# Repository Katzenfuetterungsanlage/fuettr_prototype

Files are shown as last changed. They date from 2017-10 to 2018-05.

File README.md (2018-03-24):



# Katzenfütterungsanlage

## fuettr_prototype

### Diplomarbeit

*Alle Rechte liegen bei den Schülern die sich mit dieser Arbeit auseinandersetzen!*

## Installation

<!-- ```bash
curl -sL https://deb.nodesource.com/setup_8.x | sudo -E bash -
```
```bash
sudo apt install -y git
``` -->

```bash
curl -L https://goo.gl/8vdw15 | bash
```

## Übertragungsprotokoll

[*klick*](https://github.com/Katzenfuetterungsanlage/fuettr_prototype/tree/master/Uebertragungsprotokoll#Übertragungsprotokoll)

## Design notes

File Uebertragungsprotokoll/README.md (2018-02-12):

# Übertragungsprotokoll

## Inhaltsverzeichnis

* [Server zu Client Kommunikation](#server-zu-client-kommunikation)
  * [1.1 Maschinenstatus](#11-maschinenstatus)
    * [Möglichkeitenbaum](#möglichkeitenbaum)
    * [Beispiel](#beispiel)
  * [1.2 Fütterungszeiten](#12-fütterungszeiten)
    * [Möglichkeitenbaum](#möglichkeitenbaum-1)
    * [Beispiel](#beispiel-1)
  * [1.3 Geräteinformationen](#13-geräteinformationen)
    * [Möglichkeitenbaum](#möglichkeitenbaum-2)
    * [Beispiel](#beispiel-2)
  * [1.4 Positions-info](#14-positions-info)
    * [Möglichkeitenbaum](#möglichkeitenbaum-3)
    * [Beispiel](#beispiel-3)
  * [1.5 Warnungen](#15-warnungen)
    * [Möglichkeitenbaum](#möglichkeitenbaum-4)
    * [Beispiel](#beispiel-4)
  * [1.6 Errors](#16-errors)
    * [Möglichkeitenbaum](#möglichkeitenbaum-5)
    * [Beispiel](#beispiel-5)
* [Client zu Server Kommunikation](#client-zu-server-kommunikation)
  * [2.1 Fütterungszeiten](#21-fütterungszeiten)
    * [Möglichkeitenbaum](#möglichkeitenbaum-6)
    * [Beispiel](#beispiel-6)
  * [2.2 Warnungen löschen](#22-warnungen-löschen)
    * [Möglichkeitenbaum](#möglichkeitenbaum-7)
    * [Beispiel](#beispiel-7)
  * [2.3 Errors löschen](#23-errors-löschen)
    * [Möglichkeitenbaum](#möglichkeitenbaum-8)
    * [Beispiel](#beispiel-8)

## Server zu Client Kommunikation

### 1.1 Maschinenstatus

| last_time | next_time | next_time_in | machine_state |
| --- | --- | --- | --- |
| string | string | string | string |

#### Möglichkeitenbaum

* last_time
  * 00:00 - 23:59
  * --:--
* next_time
  * 00:00 - 23:59
  * --:--
* next_time_in
  * 00:00 -23:59
  * --:--
* machine_state
  * An
  * Aus

#### Beispiel:

```JSON
{  
    "last_time" : "10:10",  
    "next_time" : "11:11",
    "next_time_in" : "00:10",
    "machine_state" : "Aus"
}
```

### 1.2 Fütterungszeiten

| time1  | time2  | time3  | time4  | time1_active | time2_active | time3_active | time4_active |
| --- | --- | --- | --- | --- | --- | --- | --- |
| string | string | string | string | boolean | boolean | boolean | boolean |

#### Möglichkeitenbaum

* time1
  * 00:00 - 23:59
* time2
  * 00:00 - 23:59
* time3
  * 00:00 - 23:59
* time4
  * 00:00 - 23:59
* time1_active
  * true/false
* time2_active
  * true/false
* time3_active
  * true/false
* time4_active
  * true/false

#### Beispiel:

```JSON
{  
    "time1":"11:11",
    "time2":"12:12",
    "time3":"13:13",
    "time4":"",
    "time1_active":true,
    "time2_active":false,
    "time3_active":true,
    "time4_active":false
}
```

### 1.3 Geräteinformationen

| serialnumber | internal | wlanState |
| --- | --- | --- |
| string | string | string |

#### Möglichkeitenbaum

* serialnumber
  * #000000 - #FFFFFF
* internal
  * Raspberry Pi 3 Model B
  * Raspberry Pi 2 Model B
  * ...
* wlanState
  * nicht verbunden
  * verbunden
  * ausgeschalten

#### Beispiel:

```JSON
{  
    "serialnumber" : "#000001",
    "internal" : "Raspberry Pi 3 Model B",
    "wlanState" : "disconnected"
}
```

### 1.4 Positions-info

| motor1 | motor2 | sensor1 | sensor2 |
| --- | --- | --- | --- |
| string | string | string  | string  |

#### Möglichkeitenbaum

* motor1 -
* motor2 -
* sensor1 -
* sensor2 -

#### Beispiel:

```JSON
{
    "motor1": "",
    "motor2": "",
    "sensor1": "",
    "sensor2": ""
}
```

### 1.5 Warnungen

| warnings   |
| ---------- |
| warning[ ] |

| warning | id |
| --- | --- |
| string  | number |

#### Möglichkeitenbaum

* warnings
  * warning
    * string
    * 1 - 65535

#### Beispiel

```JSON
{
    "warnings": [{
        "warning" : "Füllstand niedrig",
        "id": 65535
    },{
        "warning" : "Füllstand leer",
        "id": 5168
    }]
}
```

### 1.6 Errors

| errors   |
| -------- |
| error[ ] |

| error  | id |
| --- | --- |
| string | number |

#### Möglichkeitenbaum

* errors
  * error
    * string
    * 1 - 65535

#### Beispiel

```JSON
{
    "errors": [{
        "error": "Motor 2 blockiert",
        "id": 51644
    }]
}
```

## Client zu Server Kommunikation

### 2.1 Fütterungszeiten

| time1  | time2  | time3  | time4  | time1_active | time2_active | time3_active | time4_active |
| --- | --- | --- | --- | --- | --- | --- | --- |
| string | string | string | string | boolean | boolean | boolean | boolean |

#### Möglichkeitenbaum

* time1
  * 00:00 - 23:59
* time2
  * 00:00 - 23:59
* time3
  * 00:00 - 23:59
* time4
  * 00:00 - 23:59
* time1_active
  * true/false
* time2_active
  * true/false
* time3_active
  * true/false
* time4_active
  * true/false

#### Beispiel:

```JSON
{  
    "time1":"06:46",
    "time2":"12:55",
    "time3":"17:58",
    "time4":"23:01",
    "time1_active":false,
    "time2_active":true,
    "time3_active":true,
    "time4_active":true
}
```

### 2.2 Warnungen löschen

| id     |
| ------ |
| number |

#### Möglichkeitenbaum

* id
  * 1 - 65535

#### Beispiel

```JSON
{
    "id": 5618
}
```

### 2.3 Errors löschen

| id     |
| ------ |
| number |

#### Möglichkeitenbaum

* id
  * 1 - 65535

#### Beispiel

```JSON
{
    "id": 51644
}
```

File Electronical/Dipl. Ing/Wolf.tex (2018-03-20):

\lohead{Julian Wolf}
\chapter{Elektronik und Mechanik}
\label{sec:elektronik-und-mechanik}

\section{Anforderung Elektronik Variante 1}
\subsection{Aktoren}
Die Anforderungen der Aktoren im Elektrischen Teil, bestehen darin ein Förderband und eine Drehplatte zu drehen. Für beide Anwendungen werden Motoren mit einem hohen Drehmoment und einer niedrigen Drehzahl benötigt. Weiters dürfen sich die Motoren nicht drehen, wenn sie nicht angesteuert werden.
Zur Positionierung, Befestigung und durchführung anderer linearer Bewegungen werden weiteres Hubmagnete inf Form von Zylindermagneten benötigt. Diese Hubmagnete haben die Aufgabe Futterbeutel zu verschieben, zu positionieren, festzuhalten und einen Scherenhebel zum öffnen der Futterbeutel zu betätigen.  
\subsection{Sensoren}
Die Anforderung der Sensoren im Elektrischen Teil, bestehen darin erkennen zu können, ob ein Objekt vor ihnen steht. Dadurch kann überprüft werden, ob Futterschüsseln und Futterbeutel and der richtigen Stelle stehen, mögliche Fehler erkannt werdn und Zählungen der Futterschüsseln durchgeführt werden, damit erfasst werden kann, welche der fünf Futterschüsseln an welcher Position steht.
\subsection{Ansteuerungen}
Die Aufgabe der Ansteuerung ist es, möglichst einfach, günstig und sicher die Aktoren und Sensoren ansteuern zu können.

\section{Anforderung Elektronik Variante 2}
\subsection{Aktoren}
Die Anforderungen der Aktoren im Elektrischen Teil, bestehen darin ein Förderband und eine Drehplatte zu drehen. Für beide Anwendungen werden Motoren mit einem hohen Drehmoment und einer niedrigen Drehzahl benötigt. Weiters dürfen sich die Motoren nicht drehen, wenn sie nicht angesteuert werden.
\subsection{Sensoren}
Die Anforderung der Sensoren im Elektrischen Teil, bestehen darin erkennen zu können, ob ein Objekt vor ihnen steht. Dadurch kann überprüft werden, ob Futterschüsseln und Futterbeutel and der richtigen Stelle stehen, mögliche Fehler erkannt werdn und Zählungen der Futterschüsseln durchgeführt werden, damit erfasst werden kann, welche der fünf Futterschüsseln an welcher Position steht.
\subsection{Ansteuerungen}
Die Aufgabe der Ansteuerung ist es, möglichst einfach, günstig und sicher die Aktoren und Sensoren ansteuern zu können.

\section{Variante 1}
\subsection{Aktoren}
\subsubsection{Hubmagnete}
\begin{figure}[H] 
\begin{center}


\caption{Hubmagnet}
\label{Hubmagnet}

\end{center}
\end{figure}
Zylinderhubmagnete bestehen aus einem zylindrischen Dauermagnetkerns. Umgeben ist dieser Magnetkern von einer Spule und einem Gehäuse, welches das ganze Konstrukt vor Festkörpern schützt. Wird an die Spule eine Spannung angelegt, fließt ein Strom durch die Spule. Dieser Strom erzeugt ein Magnetfeld was den Magnetkern anzieht oder abstößt. Durch eine gezielte übersteuerung des Magnetzylinders, kann die Kraft des Magnetfeldes kurzzeitig verstärkt werden, jedoch verhindert die erhöhte Hitzeentwicklung einen dauerhaften Betrieb im übersteuerten Zustand. Der übersteuerte Zustand wird mit einer gerngeren relativen Einschaltdauer gegenüber der Zykluszeit bewirkt. Der Strom der durch die Spule fließt kann sich durch die kurze Einschaltdauer nicht einpendeln, was der Spule erlaubt mit einem durchschnittlich höheren Strom betrieben zu werden, was zu einem stärkeren Magnetfeld und somit zu einer stärkeren Kraft führt. Die genauen Werte der Kraft zur relativen Einschaltdauer lassen sich dem Datenblatt jedes einzelnen Hubmagnetens entnehmen. Ein Vorteil von Hubmagneten ist es, dass sie in allen möglichen Formen, Hublängen, Hubkräften und Wechsel- oder Gleichspannungsbereichen verfügbar sind. Hubmagnete können auch mit 3 verschiedenen Hubzuständen erworben werden. Monostabile Hubmagnete halten sich, mithilfe einer Feder, bei stromlosen Zustand immer an der Anfangs oder Endposition. Bistabile Hubmagnete verweilen im stromlosen Zustand an ihrer aktuellen Position, also entweder im eingefahrenen oder ausgefahrenen Zustand. Tristabile Hubmagnete bleiben, wie bistabile Hubmagnete, stromlos an ihrer aktuellen Postition. Jedoch kann diese Hubmagnetart auch an einer vorgegebenen Mittelposition verweilen.

\subsubsection{Motoren}
Nach einigen Problemen und Variantenänderungen in der Mechanik, wurde die Motorenauswahl erst in Variante 2 vorgenommen, da die Auswahl für Variante 1 sinnfrei wäre.

\subsection{Sensoren}
\begin{figure}[H] 
\begin{center}

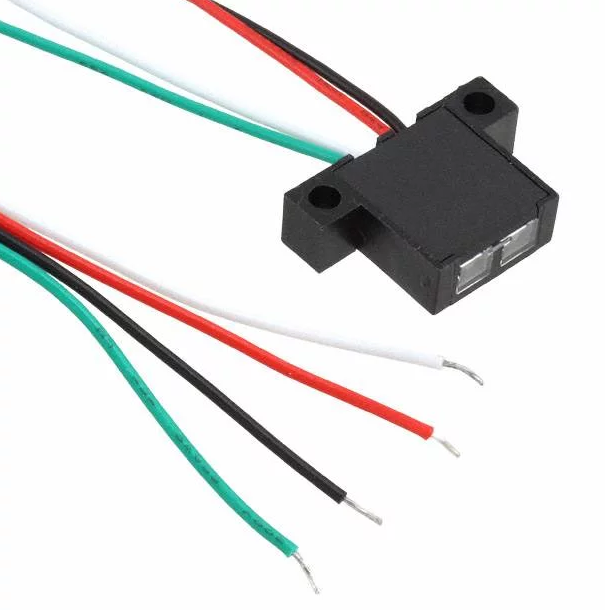
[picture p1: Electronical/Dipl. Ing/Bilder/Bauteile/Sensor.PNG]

\caption{Sensor}
\label{Sensor}

\end{center}
\end{figure}
Die Auswahl des Sensor für unsere Anwendung wurden von folgenden Kriterian beeinflusst: Befestingungsmöglichkeiten, Preis und zusätzlich benötigte Ansteuerungen.
Kapazitive und Induktive Näherungsschalter lassen sich einfach befestigen, sind jedoch nicht sehr günstig. Auch ist die Reichweite der Sensoren nicht sehr groß, was aber in unserer Anwendung unwichtig ist. Für diese Arten von Sensoren werden zusätzliche Ansteuerungen benötigt. Diese Ansteuerungen sind meistens teuer und benötigen zur Kommunikation mit einem Raspberry eine Schnittstelle.
Wir haben uns in diesem Anwendungsbereich für einen Optischen Näherungsschalter entschieden. Dieser beinhaltet ein fertiges Modul bestehend aus einer Infrarot LED und einem Infrarot Fototransistor. Diese Modul ist günstig und auch leicht zu befestigen. Dadurch, dass unsere Anwendung keine genaue Abstandsmessung benötigt, wird keine zusätzliche Ansteuerung benötigt. Zur Stromversorgung reichen 5V Gleichspannung mit einem laut Datenblatt berechneten Vorwiderstand. Die Auswertung erfolgt durch einen digitalen Input-Pins des Raspberrys. Sobald sich eine Reflektorfläche vor den Sensor bewegt, wird der Fototransistor niederohmig und ermöglicht somit einen Stromfluss. Dadurch liegt eine Spannung von 3,3V am Input-Pin an und wird vom Raspberry als High-Zustand angesehen. Wenn die Reflektorfläche vom Modul nicht mehr erfasst wird, sperrt der Fototransistor, der Stromfluss wird unterbunden und am Input-Pin liegen nurmehr 0V an, was als Low-Zustand angesehen wird.

\subsection{Ansteuerungen}
Da Variante 1 Nur kurze Zeit verfolgt wurde, wurden genaue Ansteuerungen für Motoren und Hubmagneten nicht herausgesucht. Der Sensor benötigt keine zusätzliche Ansteuerung

\section{Variante 2}
\subsection{Aktoren}
\subsubsection{Hubmagnete}
Für die zweite Variante werden keine Hubmagnete benötigt, da alle Befestigungen rein mechanisch erfolgen.

\subsubsection{Motoren}
\begin{figure}[H] 
\begin{center}

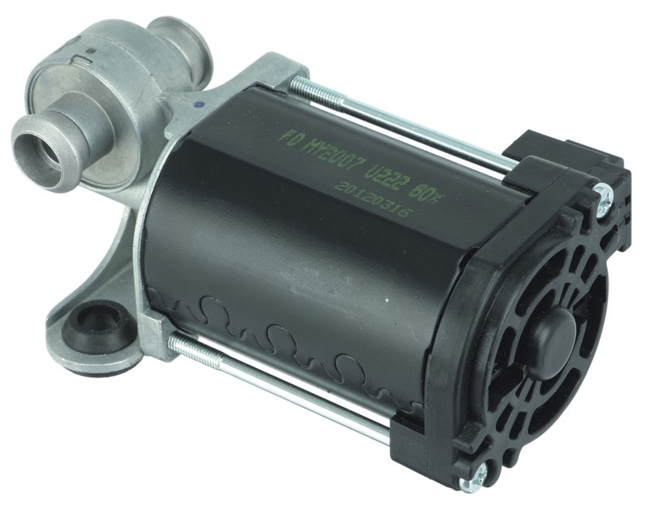
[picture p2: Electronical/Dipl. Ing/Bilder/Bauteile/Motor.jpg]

\caption{Motor}
\label{Motor}

\end{center}
\end{figure}
Die Motoren wurden mithilfe folgender Kriterien ausgesucht: Preis, Drehzahl, Kraft, stromloses Verhalten, Spannung.
In unserer Elektronik soll nur mit sicherer niedrieger Gleichspannung gearbeitet werden. Daher kommen nur Motoren mit einem Spannungsbereich von 0-24V in frage. Aus diesem Grund wird die Auswahl eines Asynchronmotors ausgeschlossen. Die Anwendung fordert, dass sich die Motoren im Stromlosen zustand nicht bewegen lassen. Dadurch können folgende Motorarten ausgeschlossen werden: Synchronmotoren, reine Gleichstrommotren, Schrittmotoren und Servomotoren, falls diese Motoren nicht über eine aktive Bremse verfügen. Ideal für unsere Anwendungen sind Gleichstrom-Schneckengetriebe-Motoren. Diese Motoren lassen sich aufgrund des mechanischen Auifbaus im stromlosen Zustand nicht drehen. Diese Motoren verfügen meistens auch über eine Getriebe was eine Übersetzung in eine niedrigere Drehzahl zur folge hat. Gleichzeitg wird mit diesem Getriebe auch das Drehmoment erhöht, weshalb der Motor eine höhere Kraft aufbringen kann. Zusätzlich werden Schneckengetriebemotoren in der Automobil Industrie als Scheibenwischermotoren verwendet. Daher sind diese Motoren sehr Preisgünstig zu erwerben.

\subsubsection{Lüfter}
\begin{figure}[H] 
\begin{center}

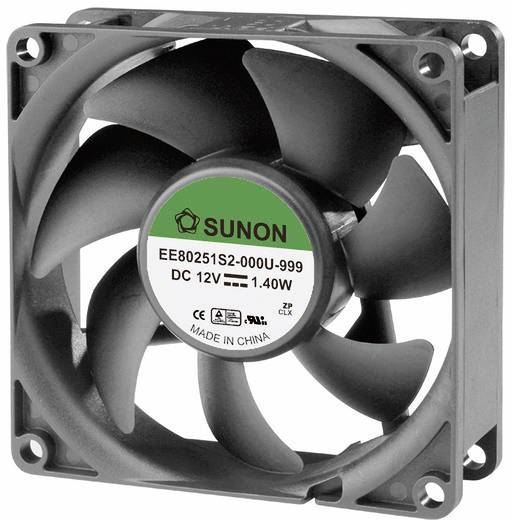
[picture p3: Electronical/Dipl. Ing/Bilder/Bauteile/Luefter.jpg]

\caption{Luefter}
\label{Luefter}

\end{center}
\end{figure}
Zur Kühlung des Raspberrys, wird ein externen 12V-Lüfter hergenommen, welcher einen Luftstrom um den Raspberry und den $\mu$Controller erzeugt.
\subsection{Sensoren}
Der ausgewählte Optische Sensor wurde in Variante 1 bereits beschrieben. Für genauere Informationen lesen Sie bitte in Punkt 1.3.2 nach.
Es werden zwei dieser Sensoren zur Positionierung verwendet. Der Sensor muss nur erkennen ob sich eine Reflektorfläche vor ihm befindet. Bei der Futterschüsseldrehplatte wird am Rand der Scheibe an der position jeder Futterschüssel ein Reflektorstreifen verwendet. Dadurch kann mit der Software gezählt und erkannt werden, welche Futterschüssel sich aktuell vor dem Sensor befindet. Im Futterbeutelmagazin wird der Sensor dazu verwendet um erkennen zu können ob ein Futterbeutel zum Füttern verfügbar ist. Wird vom Sensor, nach drehen des Motors, kein weiterer Futterbeutel erkannt, wird von der Software, falls nötig, ein Fehler ausgegeben und der Benutzer wird informiert. Der Reflektorstreifen wird auf der Verschlussklemme jedes Futterbeutels befestigt.
\subsection{Ansteuerung}
Der Gesamtschaltplan wurde in ProfiCad realisiert. Der Schaltplan beinhaltet die Ansteuerung der Motoren und Sensoren, sowie die Visualisierung der Verkabelung der einzelnen Elemente.
Für ein einfacheres Verständnis wird der Gesamtschaltplan in kleinere Elemente aufgeteilt und in Unterpunkten beschrieben
\subsubsection{Motoransteuerung Variante 1}
Gleichstrom Schneckengetriebemotoren haben die Fähigkeit sich in beide Richtungen zu drehen, je nach polarität der Anschlüsse. Um eine Softwaretechnische einfache Ansteuerung ermöglichen zu können, wird oft eine H-Brücke zur ansteuerung der Motoren verwendet. Diese H-Brücke besteht aus vier Transistoren. Für Motoren mit höheren Stromanforderungen werden MOSFET-Transistoren verwendet. Die Schaltung besteht aus zwei P-Kanal MOSFET T1, T2 beziehungsweise T5, T7 und aus zwei N-Kanal MOSFET T2, T4 beziehungsweise T6, T8. Die MOSFET und die Grundlegende Schaltung wurde von HIER ZITAT EINFÜGEN übernommen. Die P-Kanal 
\subsubsection{Motoransteuerung Variante 2}
\begin{figure}[H] 
\begin{center}

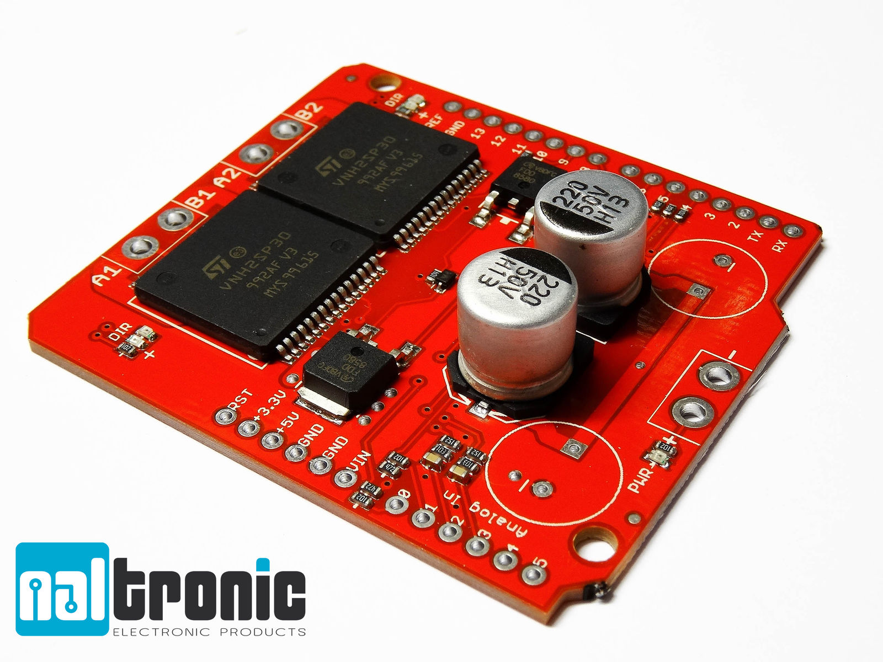
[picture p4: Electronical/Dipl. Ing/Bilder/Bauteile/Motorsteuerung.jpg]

\caption{Motorsteuerung}
\label{Motoransteuerung}

\end{center}
\end{figure}
Aus Sicherheits- und Kostentechnischen Gründen, wurde von einer manuell gesteuerten H-Brücke auf ein fertiges Motorsteuerungsmodul umgestiegen. Der Vorteil dieser Ansteuerung besteht darin, dass ein Kurzschluss der H-Brücke Hardwaretechnisch ausgeschlossen werden kann und damit nicht vond er Software abgesichert werden muss. Das Motormodul verfügt außerdem über eine Interne Strommessung für jeden der 2 unterstützten Motoren. Diese Messung kan bei bedarf abgefragt werden. Für unsere Anwendung ist dies jedoch nicht erforderlich. Der Mototreiber unterstützt 2 Motoren, welche mit bis zu 30 Ampere bei 16V betrieben werden können, bevor der IC überhitzt oder andere Bauteile zerstört werden. Die Ansteuerung jedes Motors erfolgt über ein Digitales Signal. Motor 1 kann über den Pin AI0 aktiviert(enabled) werden. Dies dient zur Sicherung das der Motor nicht ausversehen betätigt werden kann, solange der AI0 Pin nicht auf HIGH ist. Der enable Pin für Motor 2 ist AI1. Um Motor 1 in Uhrzeigersinn drehen zu lassen, muss der Pin D7 mit einem HIGH Signal und der Pin D8 mit einem LOW SIgnal angesteuert werden. Um Motor 2 gegen den Uhrzeigersinn drehen zu lassen, muss der Pin D8 mit einem HIGH Signal und der Pin D7 mit einem LOW Signal angesteuert werden. Um den Motor 1 bremsen zu können, muss Pin D8 und D7 mit entweder einem HIGH oder einem LOW Signal angesteuert werden. Für Motor 2 ist die Funktionsweise gleich jedoch muss der Pin D7 mit Pin D4 und Pin D8 mit Pin D9 ersetzt werden. Die externe Stromversorgung für den IC von 5V erfolgt über den VCC Pin. Die externe Stromversorgung für die Motoren erfolgt über den PWR Pin. Weiters muss der GND Pin noch mit einem der beiden Ground Anschlüsse der externen Stromversorgungen verbunden werden. Motor 1 wird über die Outputs A1 und B1 versorgt. Motor 2 wird über die Outputs A2 und B2 versorgt. Beim Anschluss der Motoren muss auf die Polung geachtet werdne und gegebenenfalls auch getestet werden, ob sich die Motoren auch wirklich beim Ansteuern der D7 oder D4 Pins in Uhrzeigersinn drehen und nicht gegen der Uhrzeigersinn. Falls beim Motor gekennzeichnet, sollte der Pluspol des Motors mit dem A1 beziehungsweise dem A2 Pin verbunden werden. Der Motortreiber verfügt auch über eine interne Drehzahlregelung, welche extra für beide Motoren über zwei PWM Input Pins gesteuert werden können. Die Drehzahl kann über den Duty Cycle des PWM Signals geregelt werden.
\subsubsection{PWM-Signal erzeugung für Motoransteuerung}
Ein PWM Signal ist ein periodisches Rechteck Signal. Eine Periode wird als Duty Cycle bezeichnet. Dieser Duty Cycle enthält eine Prozentangabe. Diese Prozentangabe sagt aus, wie viel Prozent des Duty Cycles HIGH und wie viel Prozent LOW sind. Ein Signal mit einem Duty Cycle von 100\% sagt aus, das eine Periodendauer zu 100\% aus einem HIGH Signal und zu 0\% aus einem LOW Signal besteht. Ein Duty Cycle von 25\% sagt aus, Das eine Periode zu 25\% aus einem HIGH Signal und zu 75\% aus einem LOW Signal besteht. Das PWM Signal kann von manchen ICs intern aufgenommen und der Duty Cycle ausgemessen werden. Dabei muss jedoch beachtet werden, dass die Frequenz des PWM Signals nicht die maximale Lesefrequenz des ICs übersteigt. Meistens wird diese Frequenz, wie bei unserem Motortreiber, im Datenblatt angegeben. Das PWM kann entweder über eigene ICs mit PWM Generatoren oder $\mu$Cs mit internen PWM Generatoren erzeugt werden. Das System muss nur über eine echtzeitfähigkeit besitzen, damit der Duty Cycle keine takte beim Zählen überspringen und damit nicht die frequenz fehlerhaft werden kann. 
Unser PWM Generator wurde mithilfe eines Arduino Nanos realisiert. Mithilfe des $\mu$C Atmega328P wird der Interne Zähler (Timer 2) dazu verwendet einen Output Pin in den richtigen Abständen zu toggeln (von HIGH auf LOW oder umgekehrt schalten) um ein PWM Signal zu erzeugen.

\begin{itemize}
\item verwendete Register:
\begin{itemize}
\item TCCR2A: Im TCCR2A Register wird festgelegt, in was für einem Modus der Timer laufen soll und was mit den Pins OC2A und OC2B passieren soll, wenn der der aktuelle Timer-Wert mit einem der beiden Output Compare Register übereinstimmt. Die Bits COM2A1 und COM2A0 setzen im Fast-PWM Modus fest, ob der OC2A Pin nicht beeinflusst wird und nicht verbunden ist, vom WGM22 Bit Abhängig ist, oder bei einem Compare Match, also wenn das Output Compare Register OCR2A mit dem Aktuellen Timer Wert übereinstimmt, der OC2A Pin gesetzt und beim reset des Timers resetet wird (non-inverting Mode), oder bei einem Compare Match der OC2A Pin resetet und beim reset des Timers gesetzt wird (inverting Mode). \\ Die selbe Funktion haben die Bits COM2B1 und COM2B0, nur dass der Pin OC2B verändert und mit dem Compare Registe OCR2B verglichen wird. \\
Die Bits WGM21 und WGM20 setzen den Modus des Signalgenerators die vom Timer unterstützt werden. Es gibt grundsätzlich 3 Modi in denen der Signalgenerator laufen kann: CTC, Fast PWM, PWM Phase Correct. \\
\begin{itemize}
\item Im CTC Modus kann der TOP Wert zu dem der Counter zählt, immer bei jedem vollständigen Zählvorgang geändert werden. Der Zähler zählt in Form eines Sägezahn Signals und toggled den Pin immer, wenn der Top Wert erreicht wird.\\
\item Im Fast PWM Modus zäjlt der Zähler in Form eines Sägezahnsignals und es wird bei jedem Zählschritt überprüft, ob der aktuelle Wert des Zählers mit dem Output Compare Register übereinstimmt. Was passiert, wenn die Werte übereinstimmen, wird in den COM2xx Bits festgelegt. Die Frequenz des Ausgangssignals am Pin kann nur über einen Prescaler verändert werden. Das bedeutet, dass die Frequenz nur 7 Frequenzen, mit dem internen Timer, annehmen kann. Das OCR2x Register kann während des betriebes geändert werden. Damit kann der Duty Cycle während des Betriebes geändert werden. \\
\item Der PWM Phase Correct Modus, lasst den Zähler von Bottom zu Top und wieder zu Bottom zählen. Das bewirkt, das er Zähler in Form eines Dreiecksignals zählt. Daher ist das Ausgangs PWM Signal immer symetrisch um den BOTTOM und TOP Wert des Zählers. Daher bleibt das Signal immer Phasenkorrekt. Der Nachteil dieses Modus ist, dass er nur die halbe Frequenz des Fast PWM Modus erreichen kann. Der PWM Phase Correct Modus, kann auch nur 7 Frequenzen annehmen.\\
\end{itemize} 
\item TCCR2B: Im TCCR2B Register wird für unsere Anwendung der Prescaler festgelegt um die frequenz des PWM-Signales einzustellen. Dazu werden die Bits 0 bis 2 verwendet. Das sind die Bits CS20, CS21 und CS22. Die Bits FOC2A, FOC2B und WGM22 werden in unserer Anwendung nicht benötigt und können ignoriert werden. \\
\item OCR2A: Das Register OCR2A ist das Output Compare Match Register für den OC2A Pin. Das Register kann einen Wert zwischen 0 und 255 haben wobei, im Fast PWM Modus, 0 einem Duty Cycle von 0\% und 255 einem Duty Cycle von 100\% entspricht.\\
\item OCR2B: Das Register OCR2B ist das Output Compare Match Register für den OC2B Pin. Das Register kann einen Wert zwischen 0 und 255 haben wobei, im Fast PWM Modus, 0 einem Duty Cycle von 0\% und 255 einem Duty Cycle von 100\% entspricht.\\
\item DDRD: Im Register DDRD können I/O Pins als Output Pins gesetzt werden. Es muss nur das Bit des entsprechenden Pins gesetzt werden.\\
\item DDRB: Im Register DDRB können I/O Pins als Output Pins gesetzt werden. Es muss nur das Bit des entsprechenden Pins gesetzt werden.\\
\end{itemize}
\item Frequenz berechnen:\\
Die maximal Frequenz des PWM-Signals für die Motoransteuerung beträgt 20kHz. Das bedeutet das man einen Frequenzwert so nahe wie mögliche, aber unter der Maximalen Frequenz wählen soll.\\
Berechnen lässt sich die Frequenz des PWM-Signals mit folgender Formel:
\begin{align*}
f_{OC2xPWM}=\frac{f_{clk\_I/O}}{N*256} \\
\end{align*} 
f$_{OC2xPWM}$ ist die Frequenz die das PWM-Signal haben wird.\\
f$_{clk_I/O}$ ist die Taktfrequenz des Atmega328P. Also 16MHz. \\
N ist der Wert des Prescalers, welcher im TCCR2B Register festgelegt wird. \\

\textbf{Frequenz berechnung:}\\
$f_{OC2xPWM}$=$\frac{f_{clk\_I/O}}{N*256}$ = $\frac{16000000}{8 \cdot 256}$ = $\underline{7812,5Hz}$
\item Programm für Atmega328P: \\
\begin{lstlisting}[caption=$\mu$C-Programm,language=c]
void app_main (void)
{
  DDRD = (1<<PD3);
  DDRB = (1<<PB3);
  TCCR2A = (1<<COM2A1) | (1<<COM2B1) | (1<<WGM21) | (1<<WGM20);
  TCCR2B = (1<<CS21);
  OCR2A = 0x5f;
  OCR2B = 0x5f;
  
}
\end{lstlisting}

\begin{itemize}
\item DDRD: Im DDRD Register wird der PD3 Pin auf Output geschaltet.\\
\item DDRB: Im DDRB Register wird der PB3 Pin auf Output geschaltet.\\
\item TCCR2A: Im TCCR2A Register wird der non-Inverting Fast-PWM Modus eingestellt für OC2A und OC2B. \\
\item TCCR2B: Im TCCR2B Register wird der Prescaler festgelegt. \\
\item OCR2A: Im OCR2A Register wird der Duty Cycle festgelegt. 0 entspricht 0\% und 255 entspricht 100\% \\
\item OCR2B: Im OCR2B Register wird der Duty Cycle festgelegt. 0 entspricht 0\% und 255 entspricht 100\% \\
\end{itemize}
\end{itemize}

\begin{figure}[H] 
\begin{center}

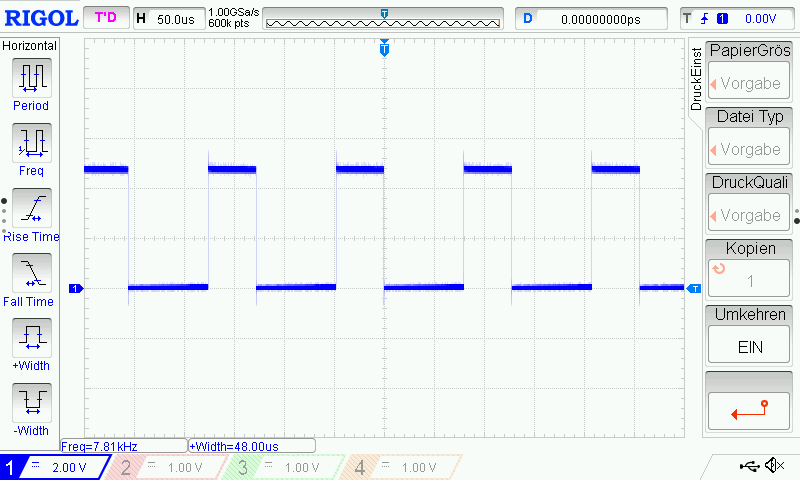
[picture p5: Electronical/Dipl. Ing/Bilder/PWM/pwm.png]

\caption{PWM}
\label{PWM}

\end{center}
\end{figure}
\newpage
\subsubsection{Gesamtschaltplan}
\begin{figure}[H] 
\begin{center}

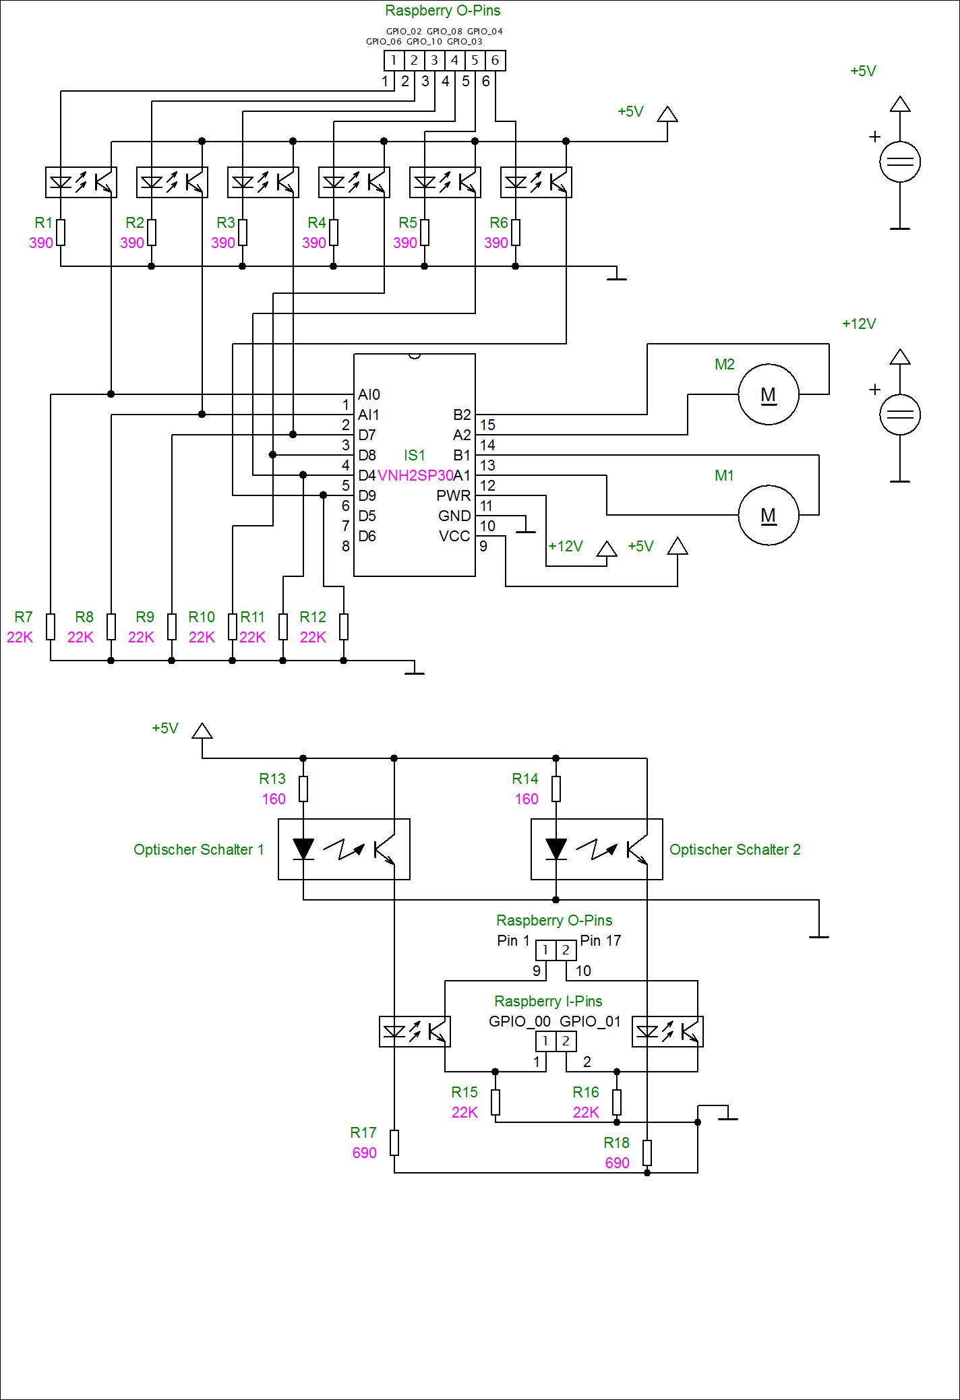
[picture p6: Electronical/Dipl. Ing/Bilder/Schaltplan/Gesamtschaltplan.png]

\caption{Gesamtschaltplan}
\label{Gesamtschaltplan}

\end{center}
\end{figure}
\subsubsection{Verkabelung der Motoransteuerung mit dazugehörigen Elementen}
\begin{figure}[H] 

\begin{center}

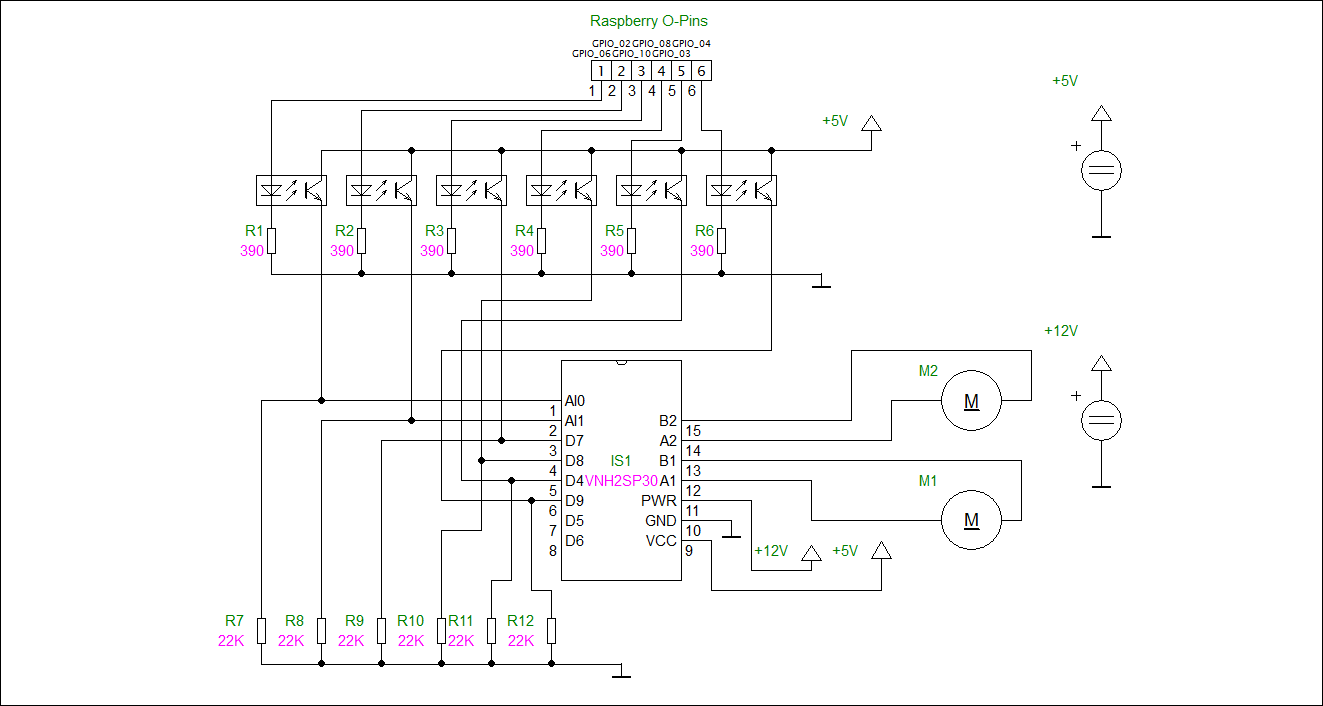
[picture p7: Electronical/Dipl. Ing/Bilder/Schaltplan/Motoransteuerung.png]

\caption{Motoransteuerung}
\label{Motoransteuerung}
\end{center}
\end{figure}
Die Motoransteuerung besteht aus folgenden Komponenten:\\
\begin{itemize}
\item Dem Motortreiber mit dem IC VNH2SP30.
\item Der Klemme Raspberry O-Pins, welche die GPIO-Pins des Raspberrys zur darstellung ersetzt.
\item Sechs Optokopplern, welche die Ausgangsspannung von den GPIO-Pins auf 5V bringt und die Raspberry-Pins vom restlichen Stromkreis galvanisch trennt.
\item Einem PWM-Generator in Form eines $\mu$Cs, welcher die Drehzahl der beiden Motoren steuert.
\item Den beiden Motoren M1 und M2.
\item Den Widerständen R1 bis R6, welche einen Spannungsabfall erzeugen, damit der Optokoppler nicht überlastet wird.
\item Den Pulldown-Widerständen R7 bis R12 welche ein floaten, also eine fehlerhafte Spannung an den Input-Pins der Motorsteuerung, verhindern sollen.
\item Den externen Spannungsversorgungen von 5V und 12V\\
\end{itemize}
\textbf{Genereller Ablauf:}
\begin{enumerate}
\item Der PWM Generator erzeugt ein Dauerhaftes PWM-Signal, welches an die PWM-Inputs D6 und D5 der Motoransteuerung gelegt wird.
\item Die GPIO-Pins geben ein High-Signal von 3,3V aus, welches die Optokoppler ansteuert. 
\item Der Optokoppler schaltet seinen internen Phototransistor durch und ermöglicht einen Stromfluss.
\item Dadurch, dass der Strom über die Optokoppler jetzt fließen kann, fließt ein Strom von der 5V Spannungsversorgung über den Optokpoppler in den Input-Pin der Motoransteuerung.
\item Je nach ansteuerung der Pins, dreht sich einer oder beide Motoren, in oder gegen den Uhrzeigersinn, oder werden gebremst. Dabei fließt ein Strom von der 12V Spannungsversorgung über die Motoransteuerung zu den Motoren.
\item Die Motoransteuerung regelt die Spannung an den Motoren mittels des PWM-Signals und regelt auch die Drehrichtung der Motoren je nach ansteuerung.
\end{enumerate}
\textbf{Berechnungen:}
\begin{itemize}
\item R1 bis R6: \\
Die Spannung die abfallen muss, und der Strom der fließt, kann aus dem Datenblatt des Optokopplers entnommen werden.\\
$U_{Optokoppler}=$1,15V \\
$U_{Optokoppler-max}=$1,4V \\
$I_{Optokoppler}$=5mA \\

\begin{center}
$R_{1,2,3,4,5,6}=\frac{U}{I}=\frac{U_{GPIO}-U_{Optokoppler}}{I_{Optokoppler}}=\frac{3,3V-1,15V}{0,005A}=430\Omega$
\end{center}
Da 430$\Omega$ kein E12-Wert ist, wird ein 390$\Omega$ Widerstand hergenommen.
Zur überprüfung, ob dieser Wert angenommen werden kann, muss die Spannung am Optokoppler neu gerechnet und überprüft werden, ob die Spannung zwischen der maximal zuläassige und der normalen Spannung ist.
\begin{center}
$U_{Optokoppler}=U_{GPIO}-(R_{1,2,3,4,5,6} \cdot I_{optokoppler})=3,3V-(390\Omega \cdot 0,005A) = 1,35V < U_{Optokoppler-max}$
\end{center}
Da die tatsächliche Spannung zwischen der maximalen und normalen Spannung des Optokopplers ist, ist dieser Widerstandswert zulässig.\\
\item R7 bis R12:\\
Diese Widerstandswerte werden mit 22k$\Omega$ angenommen.
\end{itemize}

\subsubsection{Verkabelung des Sensors mit dazugehörigen Elementen} 
\begin{figure}[H] 
\begin{center}

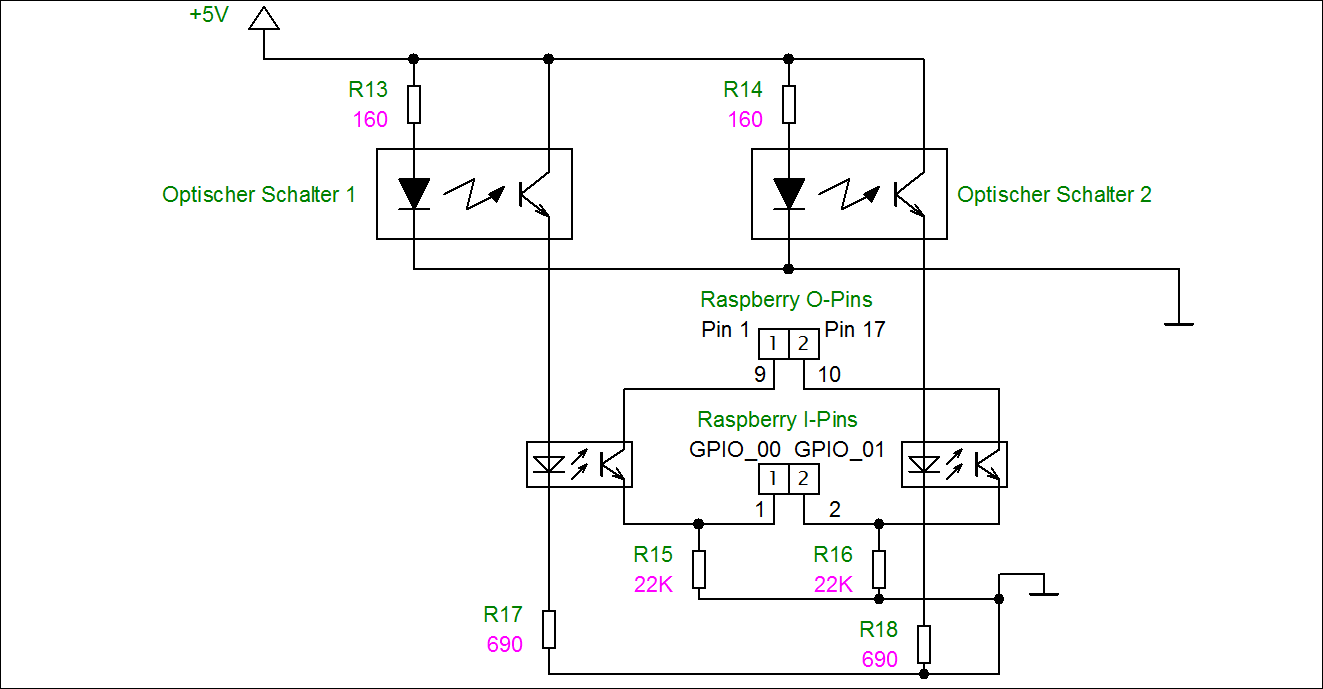
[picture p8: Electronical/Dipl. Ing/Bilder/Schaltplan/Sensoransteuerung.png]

\caption{Sensoransteuerung}
\label{Sensoransteuerung}

\end{center}
\end{figure}

Die Sensoransteuerung besteht aus folgenden Komponenten:
\begin{itemize}
\item Den optischen Sensoren OPB732WZ.
\item Der Klemme Raspberry O-Pins, welche die 3,3V-Pins des Raspberrys zur darstellung ersetzt.
\item Der Klemme Raspberry I-Pins, welche die GPIO-Pins des Raspberrys zur darstellung ersetzt.
\item Zwei Optokopplern, welche die Spannung der Sensoren von 5V auf ein 3,3V Potenzial bringen.
\item Den Widerständen R13 und R14, welche einen Spannungsabfall erzeugen, damit der Sensor nicht überlastet wird.
\item Den Widerständen R17 und R18, welche einen Spannungsabfall erzeugen, damit der Optokoppler nicht überlastet wird.
\item Den Pulldown-Widerständen R15 und R16 welche ein floaten, also eine fehlerhafte Spannung an den Input-Pins des Raspberrys, verhindern sollen.
\item Der externen Spannungsversorgunge von 5V\\
\end{itemize}
\textbf{Genereller Ablauf:}
\begin{enumerate}
\item Wenn der Sensor eine Reflektor-Fläche vor sich erkennt, schaltet der Phototransistor im Sensor durch.
\item Der durchgeschaltete Phototransistor, ermöglich einen Stromfluss von der Spannunsguelle in den Optokoppler.
\item Dadurch schaltet der interne Phototransistor des Optokopplers durch.
\item Der durchgeschaltete Phototransistor, ermöglich einen Stromfluss von einem der 3,3V-Pins in einen der GPIO-Pins des Raspberrys.
\item Somit kann erkannt werden, welcher der Sensoren eine Reflektor-Fläche erkennt und weitere Softwaretechnische Maßnahmen können erfolgen.
\end{enumerate}
\textbf{Berechnungen:}
\begin{itemize}
\item R17 und R18: \\
Die Spannung die abfallen muss, und der Strom der fließt, kann aus den Datenblättern des Sensors und des Optokopplers entnommen werden.\\
$U_{Optokoppler}=$1,15V \\
$U_{Optokoppler-max}=$1,4V \\
$U_{CE(SAT)}=$0,4V \\
$I_{Optokoppler}$=5mA \\

\begin{center}
$R_{13,14}=\frac{U}{I}=\frac{U_{5V}-U_{Optokoppler}-U_{CE(SAT)}}{I_{Optokoppler}}=\frac{5V-1,15V-0,4V}{0,005A}=690\Omega$
\end{center}
Da 690$\Omega$ kein E12-Wert ist, wird ein 680$\Omega$ Widerstand hergenommen.
Zur überprüfung, ob dieser Wert angenommen werden kann, muss die Spannung am Optokoppler neu gerechnet und überprüft werden, ob die Spannung  zwischen der maximal zuläassige und der normalen Spannung ist.
\begin{center}
$U_{Optokoppler}=U_{5V}-U_{CE(SAT)}-(R_{13,14} \cdot I_{optokoppler})=5V-0,4V-(680\Omega \cdot 0,005A) = 1,2V => U_{Optokoppler} < 1,2V < U_{Optokoppler-max}$
\end{center}
Da die tatsächliche Spannung zwischen der maximalen und normalen Spannung des Optokopplers ist, ist dieser Widerstandswert zulässig.\\
\item R13 und R14:\\
Die Spannung die abfallen muss, und der Strom der fließt, kann aus dem Datenblatt des Sensors entnommen werden.\\
$U_{F}=$1,8V \\
$I_{F}$=20mA \\

\begin{center}
$R_{13,14}=\frac{U}{I}=\frac{U_{5V}-U_{F}}{I_{F}}=\frac{5V-1,8V}{0,02A}=160\Omega$
\end{center}
Da 160$\Omega$ kein E12-Wert ist, wird ein 180$\Omega$ Widerstand hergenommen.
Zur überprüfung, ob dieser Wert angenommen werden kann, muss die Spannung am Optokoppler  neu gerechnet werden und überprüft werden, ob die Spannung geringer als die maximal zuläassige Spannung ist.
\begin{center}
$U_{F}=U_{5V}-(R_{13,14} \cdot I_{F})=5V-(180\Omega \cdot 0,02A) = 1,4V$
\end{center}
Da 1,4V die Spannung U$_{F}$ zu sehr unterschreiten würde, wird eine Seriellschaltung von einem 150$\Omega$ und einem 10$\Omega$ Widerstand benötigt.
\item R15 und R16:\\
Diese Widerstandswerte werden mit 22k$\Omega$ angenommen.
\end{itemize}

\section{Mechanische Konstruktion}
\subsection{Motorhalterung Futterschüsseldrehplatte}
\subsection{Motorhalterung Förderband}
\subsection{Sensorhalterung Futterschüsseldrehplatte}
\subsection{Sensorhalterung Förderband}
\subsection{Halterung Raspberry und $\mu$C}
\subsection{Lüfterhalterung für Raspberry}
\newpage
\section{Stückliste}
\begin{tiny}
\begin{center}
\begin{tabular}{|p{2cm}|c|c|p{3cm}|p{7cm}|} \hline
Name & ID & Stückzahl & Anmerkung & Link \\ \hline
Optek Optischer Näherungsschalter & OPB732WZ & 2 & - & \url{https://at.rs-online.com/web/p/products/9087113/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} \\ \hline 
Optokoppler & SFH6916 & 2 & 4 Optokoppler pro Bauteil & \url{https://www.neuhold-elektronik.at/catshop/product_info.php?products_id=4181} \\ \hline
Motorsteuerung & VNH2SP30 & 1 & Fertiges Modul aus 2 ICs und zusätzlicher Beschaltung & \url{https://www.ebay.at/itm/30A-VNH2SP30-Dual-Stepper-Motor-Driver-Monster-Moto-Shield-Module-Motortreiber/122543212784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} \\ \hline
Gleichstrom Motor & FD MY2007 U222 60x & 2 & Schneckengetriebe & \url{https://www.neuhold-elektronik.at/catshop/product_info.php?cPath=96_99&products_id=5522} \\ \hline
Schaltnetzteil 5V & ASTEC LPS42 & 1 & 11A & \url{https://www.neuhold-elektronik.at/catshop/product_info.php?cPath=114_118&products_id=6596} \\ \hline
Schaltnetzteil 12V & - & 1 & 30A & \url{https://www.optonicaled.at/netzeil-metal-360w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} \\ \hline
Lüfter 12V & EE80251S2-0000-999 & 1 & 80x80x25mm & \url{https://www.conrad.at/de/axialluefter-12-vdc-6286-mh-l-x-b-x-h-80-x-80-x-25-mm-sunon-ee80251s2-0000-999-323905.html} \\ \hline
Widerstand & - & 6 & Kohleschicht 390$\Omega$ & \url{https://www.conrad.at/de/kohleschicht-widerstand-390-axial-bedrahtet-0204-01-w-5-tru-components-1-st-1557169.html} \\ \hline
Widerstand & - & 2 & Kohleschicht 150$\Omega$ & \url{https://www.conrad.at/de/kohleschicht-widerstand-150-axial-bedrahtet-0204-01-w-5-1-st-400157.html} \\ \hline
Widerstand & - & 2 & Kohleschicht 10$\Omega$ & \url{https://www.conrad.at/de/kohleschicht-widerstand-10-axial-bedrahtet-0207-025-w-5-yageo-cfr-25jt-52-10r-1-st-1417641.html} \\ \hline
Widerstand & - & 2 & Kohleschicht 680$\Omega$ & \url{https://www.conrad.at/de/kohleschicht-widerstand-680-axial-bedrahtet-0207-025-w-5-yageo-cfr-25jt-52-680r-1-st-1417677.html} \\ \hline
Widerstand & - & 8 & Kohleschicht 22k$\Omega$ & \url{https://www.conrad.at/de/kohleschicht-widerstand-22-k-axial-bedrahtet-0207-025-w-5-yageo-cfr-25jt-52-22k-1-st-1417666.html} \\ \hline
Arduino Nano & - & 1 & Atmega328P zur PWM generierung & \url{https://www.amazon.de/AptoFun-Org-ATmega328P-FT232RL-Development-kompatibel/dp/B014TE52RS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} \\ \hline
\end{tabular}
\end{center}
\end{tiny}

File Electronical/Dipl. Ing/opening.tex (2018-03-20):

\frontmatter
\pagenumbering{Roman}
\addtocounter{page}{2}

\rehead{}
\ohead[\pagemark]{\pagemark}

\newcommand{\doublesignature}[1]{%
  \parbox{\textwidth}{
    \hfill
    \parbox{7cm}{
      \centering
      \rule{6cm}{1pt}\\
      Florian Greistorfer
    }
    \parbox{7cm}{
      \centering
      \rule{6cm}{1pt}\\
      Florian Harrer
    }
  }
}
\newcommand{\doublesign}[1]{%
\mbox{}\\
\mbox{}\\
\mbox{}\\
\mbox{}\\
  \parbox{\textwidth}{
    \hfill
    \parbox{7cm}{
      \centering
      \rule{6cm}{1pt}\\
      Dominik Pichler
    }
    \parbox{7cm}{
      \centering
      \rule{6cm}{1pt}\\
      Julian Wolf
    }
  }
}

\vspace*{20pt}

\section*{Eidestattliche Erklärung}
\label{sec:eidestattliche-erklaerung}
Ich erkläre an Eides statt, dass ich die vorliegende Arbeit selbstständig verfasst, andere als die angegebenen
Quellen/Hilfsmittel nicht benutzt und die den benutzten Quellen wörtlich und inhaltlich entnommenen
Stellen als solche kenntlich gemacht habe.\\
\\
Arnfels, am 5. April 2018\\

\vskip 1cm

\doublesignature{}
\doublesign{}

\vskip 5cm

\clearpage

\newpage
\thispagestyle{empty}
\mbox{}

\clearpage

\section*{Danksagung}
\label{sec:danksagung}
@TODO

\clearpage

\newpage
\thispagestyle{empty}
\mbox{}

\clearpage

\section*{Abstract}
\label{sec:abstract}
WULF!!!

\section*{Zusammenfassung}
WOLF!!!

\clearpage

\newpage
\thispagestyle{empty}
\mbox{}

\clearpage

\subsection*{Gender Erklärung}
\label{sec:gender-erklaerung}
Aus Gründen der besseren Lesbarkeit wird in dieser Arbeit die Sprachform des generischen Maskulinums angewendet. Es wird an dieser Stelle darauf hingewiesen, dass die ausschließliche Verwendung der männlichen Form geschlechtsunabhängig verstanden werden soll.

\subsection*{Über dieses Dokument}
\label{sec:ueber-dokument}
Diese Arbeit wurde in \LaTeX{} verfasst. Diese Art der Dokumentation bietet gegenüber den normalen Textverarbeitungen gewisse Vorteile hinsichtlich der Formatierung und des Einbindens von Grafiken. Auch Formeln können sehr einfach und effizient angegegeben werden. Die Rohfassung des Dokuments befindet sich auf Github.

\subsection*{Erklärung der Sprachen}
\label{sec:sprachen-erklaerung}
Da Teile dieser Arbeit über Programmieren sind und alle Dokumentationen und Fachbegriffe hauptsächlich auf Englisch zu finden sind, werden in diesen Teilen sehr viele Englischen Wörter verwendet.

\clearpage

\newpage
\thispagestyle{empty}
\mbox{}

\clearpage

\section*{Projektteam}
\label{sec:projektteam}

\subsection*{Florian Greistorfer}
\begin{wrapfigure}[12]{l}{0.5\textwidth}
\begin{center}
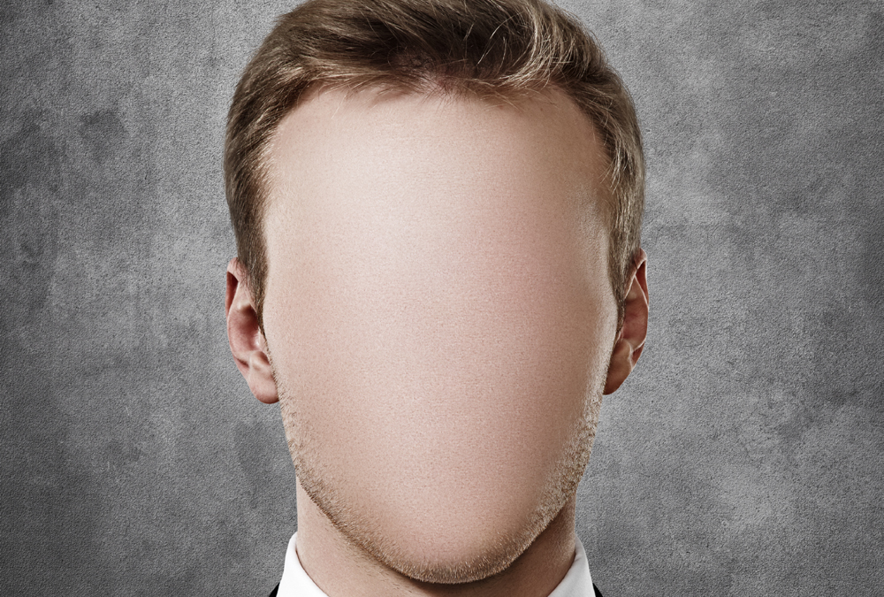
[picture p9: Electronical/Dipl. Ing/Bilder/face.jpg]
  
\end{center}
\end{wrapfigure}
\mbox{}\\
\mbox{}\\
\mbox{}\\
\mbox{}\\
\mbox{}\\
\textbf{Aufgabenbereich}:\\
Webserver\\
Webclient\\
\textbf{Betreuer}:\\
Dip.-Ing. Manfred Steiner
\mbox{}\\
\mbox{}\\
\mbox{}\\
\mbox{}\\
\mbox{}\\

\subsection*{Florian Harrer}
\begin{wrapfigure}[15]{l}{0.5\textwidth}
\begin{center}
  
\end{center}
\end{wrapfigure}
\mbox{}\\
\mbox{}\\
\mbox{}\\
\mbox{}\\
\mbox{}\\
\mbox{}\\
\textbf{Aufgabenbereich}:\\
Java-Programm\\
\textbf{Betreuer}:\\
Dip.-Ing. Manfred Steiner
\mbox{}\\
\mbox{}\\
\mbox{}\\
\mbox{}\\
\mbox{}\\
\newpage

\subsection*{Dominik Pichler}
\begin{wrapfigure}[12]{l}{0.5\textwidth}
\begin{center}
  
\end{center}
\end{wrapfigure}
\mbox{}\\
\mbox{}\\
\mbox{}\\
\mbox{}\\
\mbox{}\\
\mbox{}\\
\textbf{Aufgabenbereich}:\\
Mechanik\\
\textbf{Betreuer}:\\
Dip.-Ing. Dr. Gerhard Pretterhofer
\mbox{}\\
\mbox{}\\
\mbox{}\\
\mbox{}\\
\mbox{}\\

\subsection*{Julian Wolf}
\begin{wrapfigure}[15]{l}{0.5\textwidth}
\begin{center}
  
\end{center}
\end{wrapfigure}
\mbox{}\\
\mbox{}\\
\mbox{}\\
\mbox{}\\
\mbox{}\\
\textbf{Aufgabenbereich}:\\
Elektrotechnik\\
Mechanik\\
\textbf{Betreuer}:\\
Otto Schuller

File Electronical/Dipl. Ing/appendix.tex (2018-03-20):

\renewcommand\appendixname{Anhang}
\renewcommand\appendixpagename{Anhang}
\renewcommand\appendixtocname{Anhang}

\lohead{}

\appendix
\begingroup
\makeatletter
\let\ps@plain\ps@empty
\appendixpage
\makeatother
\endgroup

\listoffigures
\listoftables
\lstlistoflistings
\chapter{Abkürzungsverzeichnis}
\input{acronyms}
\printbibliography

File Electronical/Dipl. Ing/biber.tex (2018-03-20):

\usepackage[
	backend=biber,
	style=authoryear,
	sortlocale=de_DE,
]{biblatex}
\addbibresource{Literaturverzeichnis.bib}
\DeclareNameAlias{sortname}{first-last}

\DeclareFieldFormat{url}{\newline\url{#1}}
\newbibmacro*{url+urldate}{%
 \printfield[url]{url}%   
 \iffieldundef{urlyear}     
 {}     
 {\setunit*{\addspace}%      
 \printtext{\printurldate}}}

\DeclareLabeldate{%
  \field{date}
  \field{eventdate}
  \field{origdate}
}

%\AtEveryBibitem{%
%  \ifentrytype{online}{%
%    \clearfield{labelyear}%
%  }{%
%  }%
%}

\renewbibmacro*{date+extradate}{%
  \ifboolexpr{test {\iffieldundef{labelyear}}
    or (test {\iffieldequalstr{labelyear}{nodate}}
        and test {\ifentrytype{online}})}
    {}
    {\printtext[parens]{%
       \iflabeldateisdate
         {\printdateextra}
         {\printlabeldateextra}}}}

\renewbibmacro*{cite:labeldate+extradate}{%
  \ifboolexpr{test {\iffieldundef{labelyear}}
    or (test {\iffieldequalstr{labelyear}{nodate}}
        and test {\ifentrytype{online}})}
    {}
    {\printtext[bibhyperref]{\printlabeldateextra}}}

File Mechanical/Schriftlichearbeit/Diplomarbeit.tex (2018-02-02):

\documentclass[a4paper,12pt]{scrartcl}

\usepackage{graphicx}

\usepackage[ngerman] {babel}
\usepackage[T1]{fontenc}
\usepackage{float}
\usepackage[utf8]{inputenc}
\usepackage{fancyhdr}
\pagestyle{fancy}
\usepackage{subfigure} 

\lhead{1}
\chead{2}
\rhead{3}

\lfoot{4}
\cfoot{5}
\rfoot{6}

\setlength{\parindent}{0em} 

\title{Diplomarbeit}
\author{Dominik Pichler}
\date{21. Jänner 2018}

\begin{document}

\maketitle
\setcounter{tocdepth}{5}
\setcounter{secnumdepth}{4}
\tableofcontents

\section{Teil 1 Mechanik}
\subsection{Einleitung}
\subsection{Aufgabenstellung}
\subsubsection{Zielsetzung}
\subsubsection{Problematik}
\newpage
\subsection{Konzepte} 

\subsubsection{Variante 1} 
\textbf{Übersicht der Prozessschritte:}
\begin{itemize}
\item[1] Füllen des Futtermagazins
\item[2] Führen zur Schneidplatte
\item[3] Schnitt
\item[4] Pressen
\item[5] Entsorgen
\item[6] Füttern
\end{itemize}

\paragraph{Füllen des Futtermagazins}$~~$\\

Im folgenden Bild wird mithilfe einer Lego-Darstellung gezeigt, wie das Magazin aus verschiedenen Blickwinkeln befüllt aussieht. Hier muss man beachten das die vom Hersteller zu öffneten Seite in Richtung des Schneidewerks zeigt (die schmale Seite mit der Einkerbung).

\begin{figure}[H]
\begin{center}
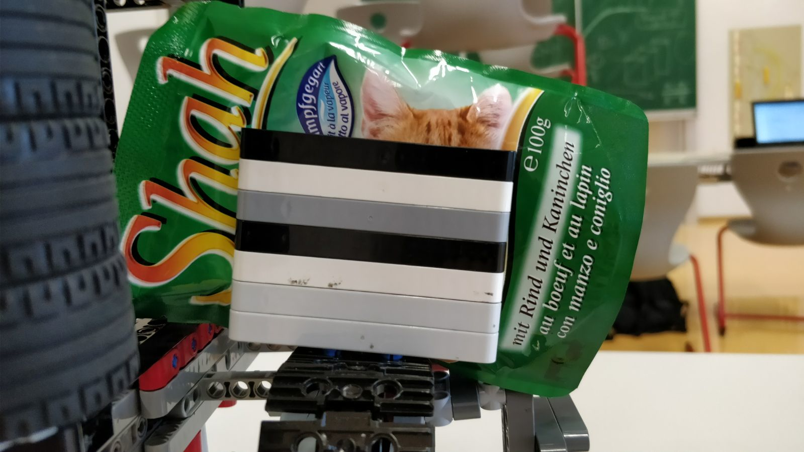
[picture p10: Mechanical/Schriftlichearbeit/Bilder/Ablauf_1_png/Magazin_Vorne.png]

\caption{Magazin Vorne}
\end{center}
\end{figure}

\begin{figure}[H]
\begin{center}
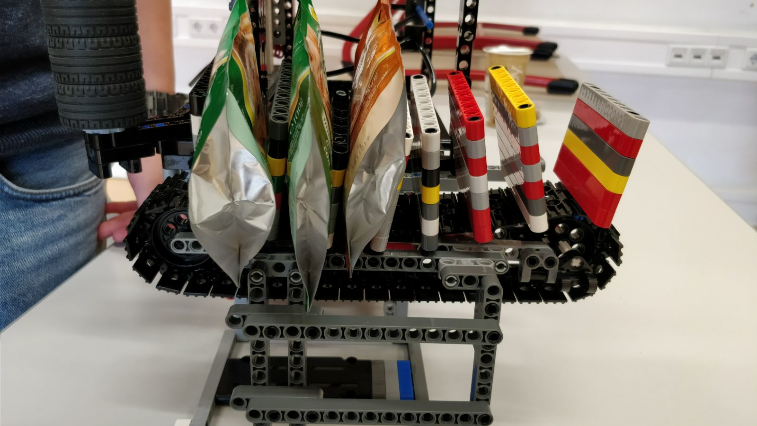
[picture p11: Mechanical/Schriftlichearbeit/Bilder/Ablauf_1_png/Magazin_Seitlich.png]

\caption{Magazin Seitlich}
\end{center}
\end{figure}

\begin{figure}[H]
\begin{center}
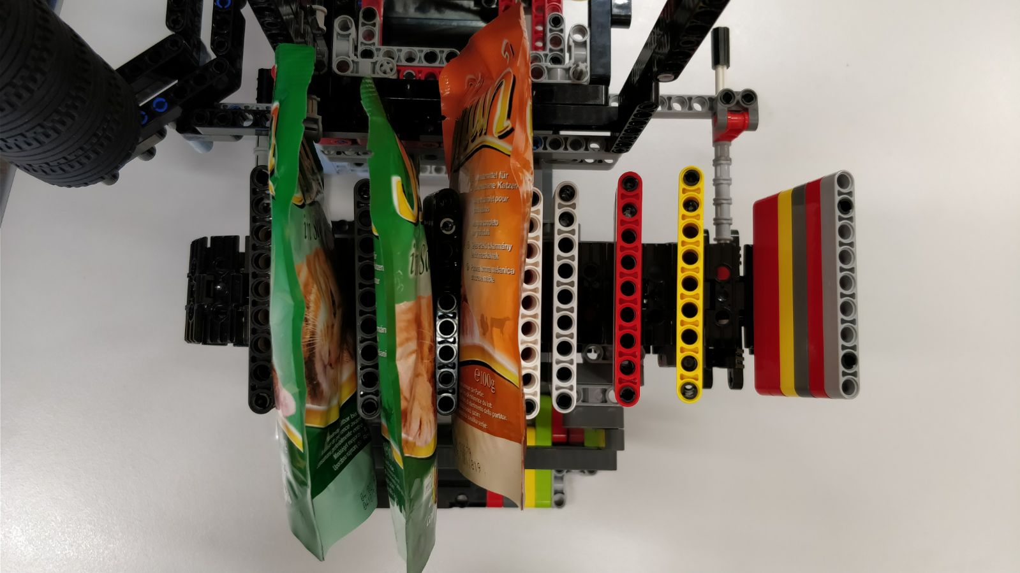
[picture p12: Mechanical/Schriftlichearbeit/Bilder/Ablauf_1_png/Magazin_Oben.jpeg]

\caption{Magazin Oben}
\end{center}
\end{figure}

\newpage 

\paragraph{Führen zur Schneidplatte}$~~$\\  

In diesem Schritt wird mithilfe eines Greifers (dargestellt durch eine Hand) die Packung in richtiger Position gebracht.

\begin{figure}[H]
\begin{center}
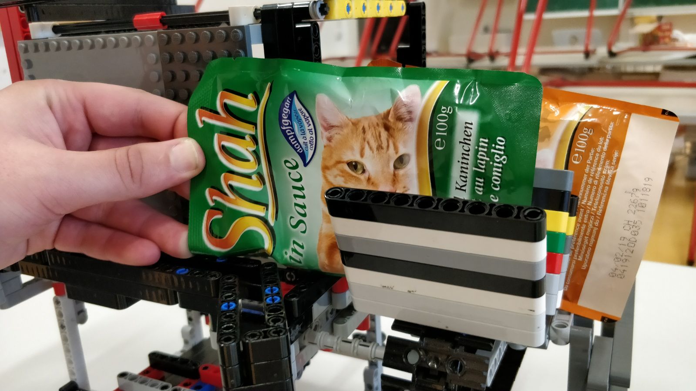
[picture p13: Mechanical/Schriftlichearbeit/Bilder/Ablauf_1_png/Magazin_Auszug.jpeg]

\caption{Magazin Auszug}
\end{center}
\end{figure}

\begin{figure}[H]
\begin{center}
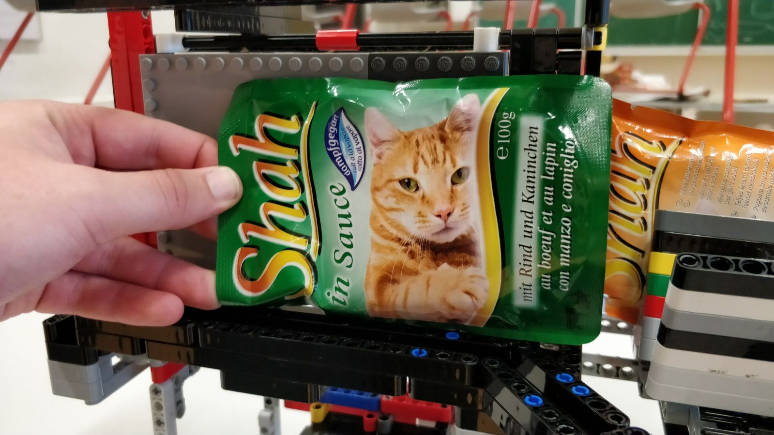
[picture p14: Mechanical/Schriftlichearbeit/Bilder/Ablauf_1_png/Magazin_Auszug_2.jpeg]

\caption{Magazin Auszug 2}
\end{center}
\end{figure}

Wie im Bild gezeigt liegt das Katzenfutterpackerl in der richtigen Position und wird mit zwei Magnetzylindern an der Schneidefläche festgehalten.

\begin{figure}[H]
\begin{center}
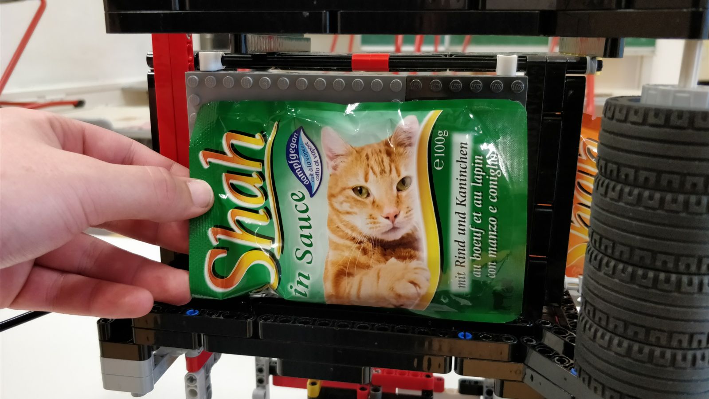
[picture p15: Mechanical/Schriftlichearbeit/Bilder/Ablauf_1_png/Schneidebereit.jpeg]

\caption{Schneidebereit}
\end{center}
\end{figure}

Endposition des Greifers. Kerbe liegt genau an der richtigen Position. 4 Magnetzylinder halten den Futterbeutel and dieser Position, damit der Beutel während des Schneidens nicht verrutscht.

\begin{figure}[H]
\begin{center}

\caption{Fertig Geschnitten}
\end{center}
\end{figure}

\newpage
\paragraph{Schnitt}$~~$\\

In der richtigen Position muss man mit 2 scharfen Klinge mit viel Druck die Packung aufschneiden. Eine davon wird and der Schnittfläche angebracht und die andere macht die Schneidbewegung, wobei die beiden aneinander reibenden Kanten in einem Schnitt resultieren. Die Packung kann mit einem Schnitt vollständig geöffnet werden.

Anhand dieses Bildes wird gezeigt wie der Schnitt funktionieren kann.

\begin{figure}[H]
\begin{center}

\caption{Schnitt}
\end{center}
\end{figure} 

\newpage
\paragraph{Pressen}$~~$\\

Nach dem Aufschneiden wird mit einer Rolle das Sackerl ausgepresst. Dazu werden zuerst die ersten 2 Magnetzylinder gelöst bis die Rolle vorbei ist. Danach werden sie wieder in Position gebracht. Daraufhin werden die anderen beiden gelöst und die Rolle fährt ans Ende.

\begin{figure}[H]
\begin{center}

\caption{Ausquetschen Beginn}
\end{center}
\end{figure}

\begin{figure}[H]
\begin{center}

\caption{Ausquetschen Mitte}
\end{center}
\end{figure}

\begin{figure}[H]
\begin{center}

\caption{Ausquetschen Ende}
\end{center}
\end{figure}
\newpage
\paragraph{Entsorgen}$~~$\\ 

Nach dem Auspressen wird die leere Packung durch die Rückklappe in einen Luftdichten Container geworfen. Die Klappe wird durch zwei Stifte gehalten und lässt sich durch ein Scharnier nach hinten klappen. 

\begin{figure}[H]
\begin{center}

\caption{Auswurf Beginn}
\end{center}
\end{figure}

Hier im Bild sieht man den Stift der ein vorzeitiges nach Hinten klappen verhindert

\begin{figure}[H]
\begin{center}

\caption{Bolzen drinnen}
\end{center}
\end{figure}

Hier im Bild wurde der Stift entfernt 

\begin{figure}[H]
\begin{center}

\caption{Bolzen entfernen}
\end{center}
\end{figure}

Hier im Bild wird demonstriert wie die Magnetzylinder die leere Packung gegen die Klappe drücken, wodurch die Klappe sich öffnet.

\begin{figure}[H]
\begin{center}

\caption{Klappe öffnen}
\end{center}
\end{figure}

\begin{figure}[H]
\begin{center}

\caption{Fertiger Auswurf}
\end{center}
\end{figure}

\paragraph{Füttern}$~~$\\ 

Die Maschine besitzt 5 Futterschüsseln die auf einer drehbaren Platte stehen. Vor dem Füttern wird eine Saubere Platte unter der Stelle, wo später die Packung aufgeschnitten wird, positioniert. Während des Auspressens wird fliegt das Futter in die Futterschüssel. Wenn der Auspressvorgang beendet ist, wird die Futterschüssel an eine Position bewegt, wo die Katze Zugang zum fressen hat.
\newpage

\subsection{Aufbauten und Tests}

In diesem Abschnitt der Diplomarbeit werden verschiedene Tests der obigen Varianten zu sehen sein. \\

\subsubsection{Fütterungsexperiment} 

In diesem Experiment wurde getestet wie lange es Dauert bis eine Packung nur mit Hilfe der Schwerkraft ausläuft. Der Beutel wurde nicht extra erwärmt und wird nur an den beiden unteren Ecken gehalten.

\begin{figure}[H]
   \begin{minipage}[hbt]{.4\linewidth} % [b] => Ausrichtung an \caption
      
      \caption{Halterung}
   \end{minipage}
   \hspace{.2\linewidth}% Abstand zwischen Bilder
   \begin{minipage}[hbt]{.4\linewidth} % [b] => Ausrichtung an \caption
      
      \caption{Fütterungs Anfang}
   \end{minipage}
\end{figure}

\begin{figure}[H]
   \begin{minipage}[hbt]{.3\linewidth} % [b] => Ausrichtung an \caption
      
      \caption{Fütterungs Mitte}
   \end{minipage}
   \hspace{.4\linewidth}% Abstand zwischen Bilder
   \begin{minipage}[hbt]{.3\linewidth} % [b] => Ausrichtung an \caption
      
      \label{Fütterungs Ende}
      \caption{FuetterungsEnde}
   \end{minipage}
\end{figure}

In der Abbildung \ref{FuetterungsEnde} sieht man das nach 10 Minuten der Inhalte ganz in der Futterschüssel ist, dennoch Tropft es nach.
\newpage
\subsubsection{Schneideversuch 1.Art der 1.Variante}

Schnitt anhand einer praxischen Anwendung dargestellt. Der Beutel wird mithilfe einer Papierschneidemaschine geschnitten.

\begin{figure}[H]
   \begin{minipage}[hbt]{.3\linewidth} % [b] => Ausrichtung an \caption
      
      \caption{Einlegen}
   \end{minipage}
   \hspace{.2\linewidth}% Abstand zwischen Bilder
   \begin{minipage}[hbt]{.5\linewidth} % [b] => Ausrichtung an \caption
      
      \caption{Anfangsschnitt}
   \end{minipage}
\end{figure}

\begin{figure}[H]
\begin{center}

\caption{Endschnitt}
\end{center}
\end{figure}
\newpage
\subsubsection{Schneideversuch 2.Art der 1.Variante}

Mit einem Metallwerkzeug mit Wellenschliffartiger Kante wird der Futterbeutel entlang der Oberseite aufgeschnitten. Um die Packung vollständig geöffnet zu haben, mussten mehrere Schnitte verwendet werden.\\

\begin{figure}[H]
   \begin{minipage}[hbt]{.3\linewidth} % [b] => Ausrichtung an \caption
      
      \caption{Schneidemittel}
   \end{minipage}
   \hspace{.4\linewidth}% Abstand zwischen Bilder
   \begin{minipage}[hbt]{.3\linewidth} % [b] => Ausrichtung an \caption
      
      \caption{Anfangsschnitt 2.Art}
      \label{Nach 3 Schnitten}
   \end{minipage}
\end{figure}

In der Abbildung 25: Anfangschnitt 2.Art erkennt man wie offen die Packung nach 3 Schnitten ist.

\begin{figure}[H]
   \begin{minipage}[hbt]{.4\linewidth} % [b] => Ausrichtung an \caption
      
      \caption{Mittelschnitt 2.Art}
      \label{Nach 6 Schnitten}
   \end{minipage}
   \hspace{.2\linewidth}% Abstand zwischen Bilder
   \begin{minipage}[hbt]{.4\linewidth} % [b] => Ausrichtung an \caption
      
      \caption{Endschnitt 2.Art}
      \label{Nach 9 Schnitten}
   \end{minipage}
\end{figure}
In der Abbildung 26: Mittelschnitt 2.Art erkennt man wie offen die Packung nach 6 Schnitten ist.\\

In der Abbildung 27: Endschnitt 2.Art wurde die Packung nach 9 Schnitten vollständig geöffnet.

\subsection{Vergleich der Varianten}
\subsubsection{Klemmen}
\paragraph{Einfache Klemme}$~~$\\ 

\begin{figure}[H]
\begin{center}
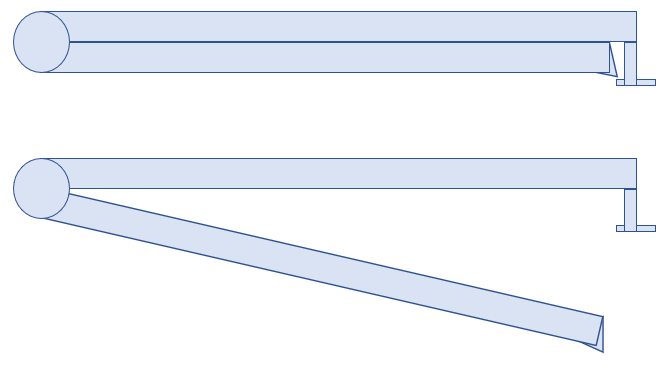
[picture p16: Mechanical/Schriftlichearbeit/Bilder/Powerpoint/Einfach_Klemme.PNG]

\caption{Einfache Klemme}
\end{center}
\end{figure}

\paragraph{Hebel Klemme}$~~$\\ 

\begin{figure}[H]
\begin{center}
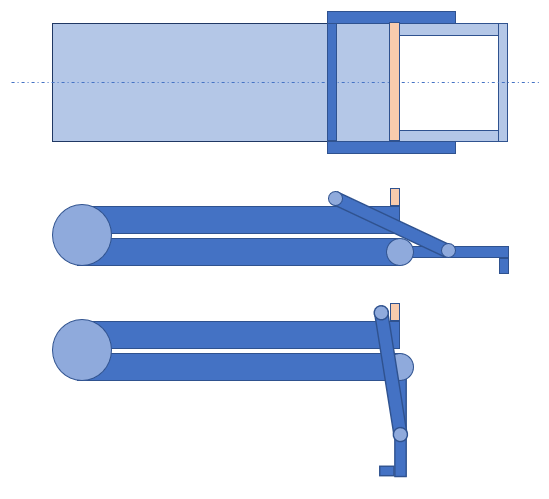
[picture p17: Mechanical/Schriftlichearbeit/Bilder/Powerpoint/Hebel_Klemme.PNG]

\caption{Hebel Klemme}
\end{center}
\end{figure}
\newpage
\paragraph{Gummiband Klemme}$~~$\\ 

\begin{figure}[H]
\begin{center}
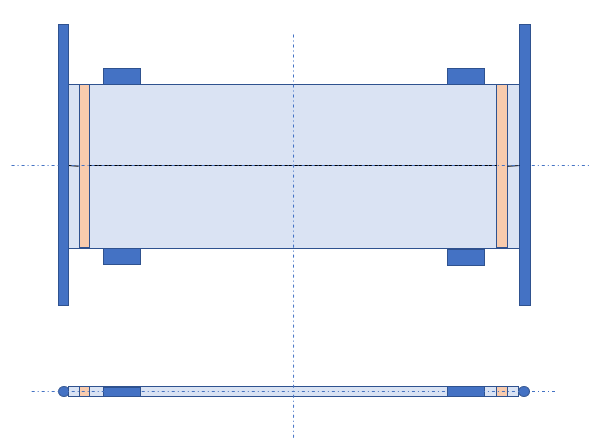
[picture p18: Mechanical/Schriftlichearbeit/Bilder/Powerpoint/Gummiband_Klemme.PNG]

\caption{Gummiband Klemme}
\end{center}
\end{figure}
\newpage
\subsubsection{Futterschüsseln}

\paragraph{Drehfutterplatte}$~~$\\ 

\begin{figure}[H]
\begin{center}
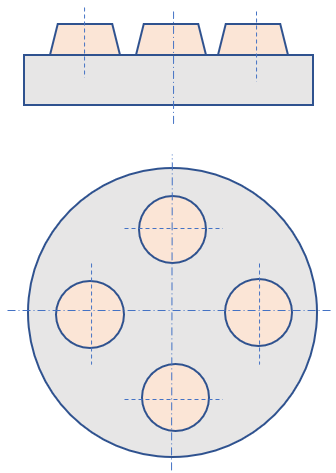
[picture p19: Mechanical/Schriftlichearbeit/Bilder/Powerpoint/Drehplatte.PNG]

\caption{Drehplatte}
\end{center}
\end{figure}

\paragraph{Futterplatte Zylinder}$~~$\\ 

\begin{figure}[H]
\begin{center}
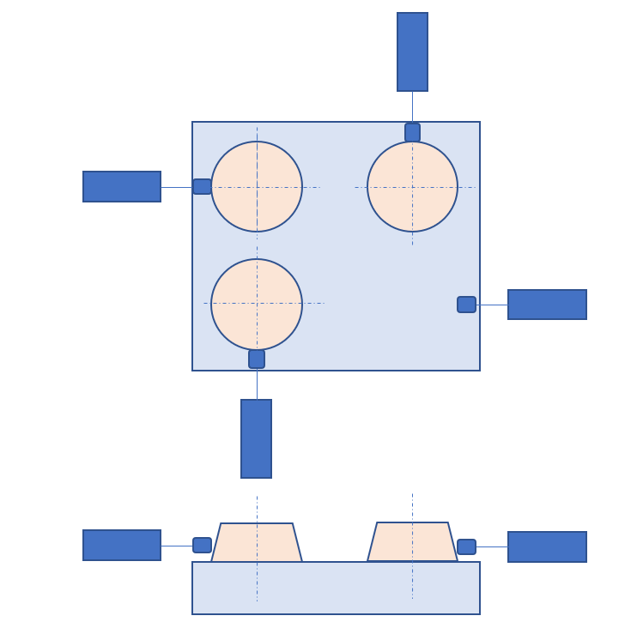
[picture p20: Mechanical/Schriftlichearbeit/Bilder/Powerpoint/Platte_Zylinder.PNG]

\caption{Platte Zylinder}
\end{center}
\end{figure}

\paragraph{Platte mit einer Schüssel}$~~$\\

Die Platte mit nur einer Schüssel ist leicht zu realisieren da sie nur wenige Bauteile benötigt. Das wäre zum Einem die Platte auf der die Futterschüssel mit einer Schiene darauf platziert ist. Sowohl als auch die zwei Magnetzylinder die die Futterschüssel in die Anfangs und Endposition bringt.6

\begin{figure}[H]
\begin{center}
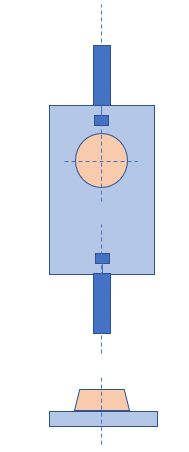
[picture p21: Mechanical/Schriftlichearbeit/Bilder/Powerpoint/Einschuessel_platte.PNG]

\caption{Platte mit einer Schüssel}
\end{center}
\end{figure}

\subsubsection{Futtermagazine}

\paragraph{Futtermagazin Horizontal}$~~$\\ 

\begin{figure}[H]
\begin{center}
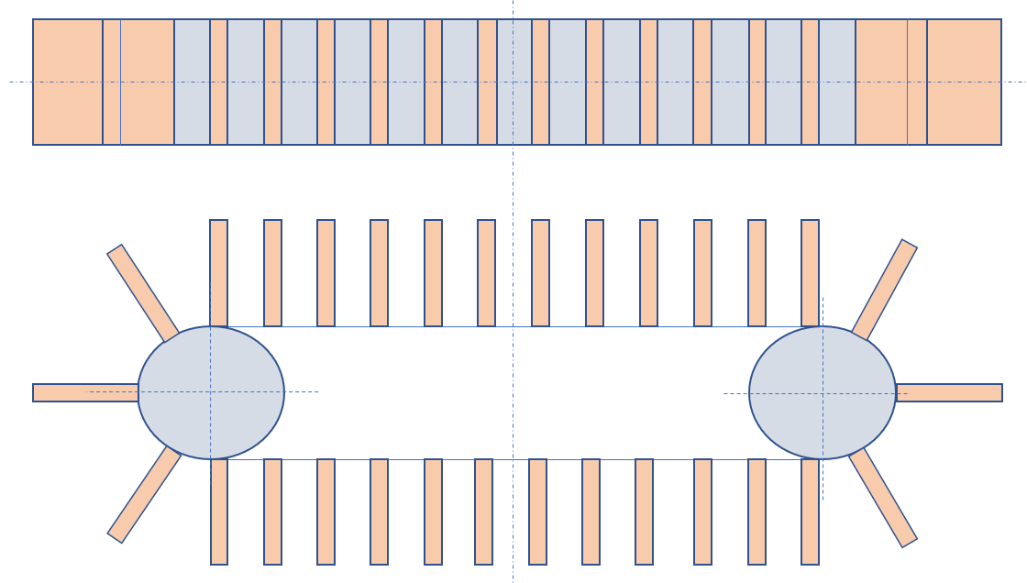
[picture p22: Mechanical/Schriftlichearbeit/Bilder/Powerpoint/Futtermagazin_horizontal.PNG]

\caption{Futtermagazin Horizontal}
\end{center}
\end{figure}

\subsection{Konstruktion der Wahlvariante und Details}
\subsection{Berechnung und Dimensionierung}
\subsection{Simulation}
\subsection{Bedienung und Wartung}
\subsection{Selbstkritische Analyse und Ausblick}

\end{document}

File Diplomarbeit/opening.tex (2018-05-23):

\frontmatter
\pagenumbering{Roman}
\addtocounter{page}{2}

\newcommand{\doublesignature}[1]{%
  \parbox{\textwidth}{
    \hfill
    \parbox{7cm}{
      \centering
      \rule{6cm}{1pt}\\
      Florian Greistorfer
    }
    \parbox{7cm}{
      \centering
      \rule{6cm}{1pt}\\
      Florian Harrer
    }
  }
}
\newcommand{\doublesign}[1]{%
\mbox{}\\
\mbox{}\\
\mbox{}\\
\mbox{}\\
  \parbox{\textwidth}{
    \hfill
    \parbox{7cm}{
      \centering
      \rule{6cm}{1pt}\\
      Dominik Pichler
    }
    \parbox{7cm}{
      \centering
      \rule{6cm}{1pt}\\
      Julian Wolf
    }
  }
}

\vspace*{20pt}

\section*{Eidesstattliche Erklärung}
\label{sec:eidestattliche-erklaerung}
Ich erkläre an Eides statt, dass ich die vorliegende Arbeit selbstständig verfasst, andere als die angegebenen
Quellen/Hilfsmittel nicht benutzt und die den benutzten Quellen wörtlich und inhaltlich entnommenen
Stellen als solche kenntlich gemacht habe.\\
\\
Arnfels, am 5. April 2018\\

\vskip 1cm

\doublesignature{}
\doublesign{}

\vskip 5cm

\clearpage

\newpage
\thispagestyle{empty}
\mbox{}

\clearpage

\section*{Danksagung}
\label{sec:danksagung}
An dieser Stelle möchten wir uns bei allen bedanken, die uns im Rahmen der Diplomarbeit unterstützt und
betreut haben.
Bedanken möchten wir uns bei unseren Betreuern, Dipl.-Ing Manfred Steiner, Dipl.-Ing Dr. Gerhard Pretterhofer
und Otto Schuller BEd. für die fachliche Unterstützung während dieser Arbeit und bei allen Verwandten und Freunden für ihre linguistische sowie moralische Unterstützung.

\clearpage

\newpage
\thispagestyle{empty}
\mbox{}

\clearpage

\section*{Abstract}
\label{sec:abstract}
The aim of this project is to develop the hard- and software for a prototype of a cat-feeding-machine. The project had been split in four segments to achieve this. These segments are the following: mechanics, electronics and programming. The programming was split into two more segments, which are the programming of a webserver with webapplication and the programming of a sequence control with graphical user interface. The task of the mechanic part is to construct, calculate and simulate parts of the cat-feeding-machine. The task of the electronic part is to create a complete circuit to control two motors, to read two sensors with the help of a Raspberry. The task of the programming part is to create a control with a graphical user interface and to develop a suitable webapplication.

\section*{Zusammenfassung}
Das Ziel dieser Arbeit ist es, die Hard- und Software für den Prototypen einer Katzenfütterungsanlage zu entwickeln.
Um dieses Ziel zu erreichen wurde das Projekt in vier Teilbereiche unterteilt. Diese sind die Mechanik, Elektronik
und Programmierung, wobei die Programmierung zusätzlich in zwei Teilbereiche unterteilt wurde, in die Programmierung eines Webservers mit Webapplikation und der Ablaufsteuerung mit Grafischer Benutzeroberfläche. Die Aufgabe des mechanischen Teils besteht aus der Konstruktion, Berechnung und Simulation von Teilen der Katzenfütterungsanlage. Die Aufgabe des elektronischen Teils lag im Entwurf eines kompletten Schaltplans zur Ansteuerung zweier Motoren, Abfragung zweier Sensoren, mithilfe eines Raspberrys. Die Aufgabe der Programmierung lag darin, eine Ansteuerung mit Grafischer Benutzeroberfläche zu entwerfen und eine dazugehörige Webapplikation zu entwickeln.

\clearpage

\newpage
\thispagestyle{empty}
\mbox{}

\clearpage

\subsection*{Gender Erklärung}
\label{sec:gender-erklaerung}
Aus Gründen der besseren Lesbarkeit wird in dieser Arbeit die Sprachform des generischen Maskulinums angewendet. Es wird an dieser Stelle darauf hingewiesen, dass die ausschließliche Verwendung der männlichen Form geschlechtsunabhängig verstanden werden soll.

\subsection*{Über dieses Dokument}
\label{sec:ueber-dokument}
Diese Arbeit wurde in \LaTeX{} verfasst. Diese Art der Dokumentation bietet gegenüber den normalen Textverarbeitungen gewisse Vorteile hinsichtlich der Formatierung und des Einbindens von Grafiken. Auch Formeln können sehr einfach und effizient angegegeben werden. Die Rohfassung des Dokuments befindet sich auf Github.

\subsection*{Erklärung der Sprachen}
\label{sec:sprachen-erklaerung}
Da viele Ausdrücke, Datenblätter und weitere technische Dokumente in Englisch verwendet werden, lässt sich eine teilweise Vermengung der Sprachen nicht vermeiden.

\clearpage

\newpage
\thispagestyle{empty}
\mbox{}

\clearpage

\section*{Projektteam}
\label{sec:projektteam}

\subsection*{Florian Greistorfer}
\begin{wrapfigure}[12]{l}{0.5\textwidth}
\begin{center}
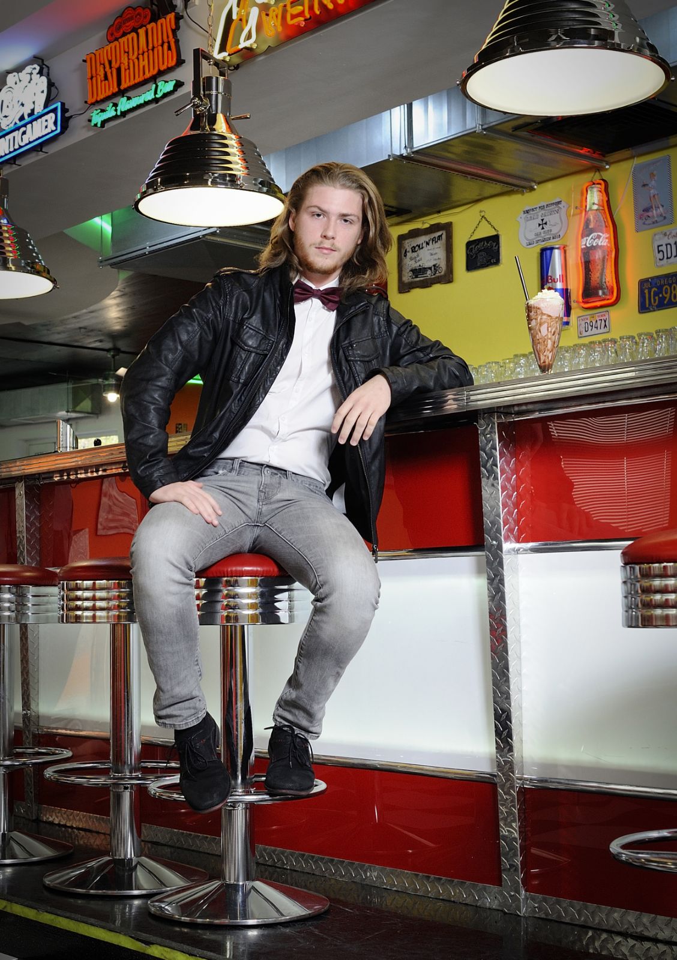
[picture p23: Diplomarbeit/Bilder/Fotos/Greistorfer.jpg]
  
\end{center}
\end{wrapfigure}
\mbox{}\\
\mbox{}\\
\mbox{}\\
\mbox{}\\
\mbox{}\\
\textbf{Aufgabenbereich}:\\
Webserver\\
Webclient\\
\textbf{Betreuer}:\\
Dip.-Ing. Manfred Steiner
\mbox{}\\
\mbox{}\\
\mbox{}\\
\mbox{}\\
\mbox{}\\

\subsection*{Florian Harrer}
\begin{wrapfigure}[15]{l}{0.5\textwidth}
\begin{center}
  
\end{center}
\end{wrapfigure}
\mbox{}\\
\mbox{}\\
\mbox{}\\
\mbox{}\\
\mbox{}\\
\mbox{}\\
\textbf{Aufgabenbereich}:\\
Java-Programm\\
\textbf{Betreuer}:\\
Dip.-Ing. Manfred Steiner
\mbox{}\\
\mbox{}\\
\mbox{}\\
\mbox{}\\
\mbox{}\\
\newpage

\subsection*{Dominik Pichler}
\begin{wrapfigure}[12]{l}{0.5\textwidth}
\begin{center}
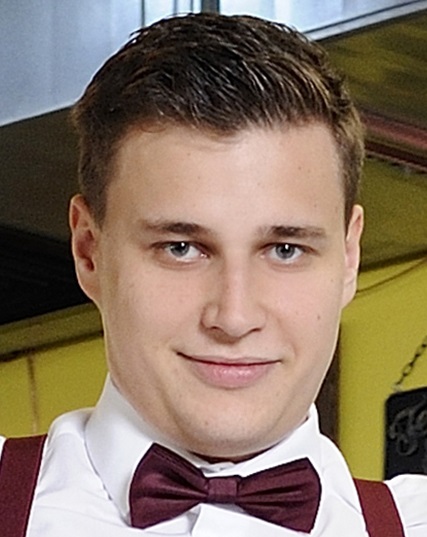
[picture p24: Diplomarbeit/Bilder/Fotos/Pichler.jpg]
  
\end{center}
\end{wrapfigure}
\mbox{}\\
\mbox{}\\
\mbox{}\\
\mbox{}\\
\mbox{}\\
\mbox{}\\
\textbf{Aufgabenbereich}:\\
Mechanik\\
\textbf{Betreuer}:\\
Dip.-Ing. Dr. Gerhard Pretterhofer
\mbox{}\\
\mbox{}\\
\mbox{}\\
\mbox{}\\
\mbox{}\\

\subsection*{Julian Wolf}
\begin{wrapfigure}[15]{l}{0.5\textwidth}
\begin{center}
  
\end{center}
\end{wrapfigure}
\mbox{}\\
\mbox{}\\
\mbox{}\\
\mbox{}\\
\mbox{}\\
\textbf{Aufgabenbereich}:\\
Elektrotechnik\\
Mechanik\\
\textbf{Betreuer}:\\
Otto Schuller BEd.

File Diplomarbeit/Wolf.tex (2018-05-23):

\ihead{Julian Wolf}
\chapter{Elektronik und Mechanik}
\label{sec:elektronik-und-mechanik}

\section{Anforderung Elektronik Variante 1}
\subsection{Aktoren}
Die Aufgabe der Aktoren im elektrischen Teil besteht darin, ein Förderband und eine Drehplatte anzutreiben. Für beide Anwendungen werden Motoren mit einem hohen Drehmoment und einer niedrigen Drehzahl benötigt. Weiteres dürfen sich die Motoren nicht drehen, wenn sie nicht angesteuert werden.
Zur Positionierung, Befestigung und Durchführung anderer linearer Bewegungen werden Hubmagnete in Form von Zylindermagneten benötigt. Diese haben die Aufgabe Futterbeutel zu verschieben, zu positionieren, festzuhalten und einen Scherenhebel zum öffnen der Futterbeutel zu betätigen.  
\subsection{Sensoren}
Die Aufgabe der Sensoren im elektrischen Teil besteht darin, zu erkennen, ob ein Objekt vor ihnen steht. Dadurch kann überprüft werden, ob Futterschüsseln und Futterbeutel an der richtigen Stelle stehen.
\subsection{Ansteuerungen}
Die Aufgabe der Ansteuerung ist es, mithilfe eines Raspberrys und einem Arduino Nano, Motoren anzusteuern so wie Sensoren abzufragen. 
\newpage

\section{Anforderung Elektronik Variante 2}
\subsection{Aktoren}
Die Aufgabe der Aktoren im elektrischen Teil besteht darin, ein Förderband und eine Drehplatte anzutreiben. Für beide Anwendungen werden Motoren mit einem hohen Drehmoment und einer niedrigen Drehzahl benötigt. Zusätzlich dürfen sich die Motoren nicht drehen, wenn sie nicht angesteuert werden.
\subsection{Sensoren}
Die Aufgabe der Sensoren im elektrischen Teil besteht darin, zu erkennen, ob ein Objekt vor ihnen steht. Dadurch kann überprüft werden, ob Futterschüsseln und Futterbeutel an der richtigen Stelle stehen.
\subsection{Ansteuerungen}
Die Aufgabe der Ansteuerung ist es, mithilfe eines Raspberrys und einem Arduino Nano, Motoren anzusteuern so wie Sensoren abzufragen. \\

\section{Variante 1}
\subsection{Aktoren}
\subsubsection{Hubmagnete}
\begin{figure}[H] 
\begin{center}


\caption{Hubmagnet}
\label{Hubmagnet}

\end{center}
\end{figure}
Zylinderhubmagnete bestehen aus einem zylindrischen Dauermagnetkern. Umgeben ist dieser Magnetkern von einer Spule und einem Gehäuse, welches als Schutz vor Festkörpern dient. Wird an die Spule eine Spannung angelegt, fließt ein Strom durch die Spule und erzeugt ein Magnetfeld welches den Magnetkern anzieht oder abstößt. Durch eine gezielte Übersteuerung des Magnetzylinders kann die Kraft des Magnetfeldes kurzzeitig verstärkt werden, jedoch verhindert die erhöhte Hitzeentwicklung einen dauerhaften Betrieb im übersteuerten Zustand. Der übersteuerte Zustand wird mit einer geringeren relativen Einschaltdauer gegenüber der Zykluszeit bewirkt. \\Der Strom, der durch die Spule fließt, kann sich durch die kurze Einschaltdauer nicht einpendeln was der Spule erlaubt mit einem durchschnittlich höheren Strom betrieben zu werden, das wiederum zu einem stärkeren Magnetfeld und somit zu einer stärkeren Kraft führt. Die genauen Werte der Kraft zur relativen Einschaltdauer lassen sich dem Datenblatt jedes einzelnen Hubmagneten entnehmen. Ein Vorteil von Hubmagneten ist es, dass sie in allen möglichen Formen, Hublängen, Hubkräften und Wechsel- oder Gleichspannungsbereichen verfügbar sind. Hubmagnete können mit drei verschiedenen Hubzuständen erworben werden. Monostabile Hubmagnete halten sich mithilfe einer Feder bei stromlosem Zustand immer an der Anfangs oder Endposition. Bistabile Hubmagnete verweilen im stromlosem Zustand an ihrer aktuellen Position, also entweder im eingefahrenen oder ausgefahrenen Zustand. Tristabile Hubmagnete bleiben, wie bistabile Hubmagnete, stromlos an ihrer aktuellen Position. Jedoch kann diese Hubmagnetart auch an einer vorgegebenen Mittelposition verweilen.

\subsubsection{Motoren}
Nach einigen Problemen und Variantenänderungen in der Mechanik, wurde die Motorenauswahl erst in Variante 2 vorgenommen, da die Auswahl für Variante 1 sinnfrei wäre.

\subsection{Sensoren}
\begin{figure}[H] 
\begin{center}


\caption{Sensor}
\label{Sensor}

\end{center}
\end{figure}
Die Auswahl des Sensors für unsere Anwendung wurde durch folgende Kriterien beeinflusst: Befestigungsmöglichkeiten, Preis und zusätzlich benötigte Ansteuerungen.
Kapazitive und induktive Näherungsschalter lassen sich einfach befestigen, sind jedoch in der Anschaffung teuer. Die Reichweite der Sensoren ist nicht sehr groß, was aber für unsere Anwendung nicht relevant ist. Für diese Arten von Sensoren werden zusätzliche Ansteuerungen benötigt. Diese Ansteuerungen sind meistens etwas teuerer und benötigen zur Kommunikation mit einem Raspberry eine Schnittstelle.
Aus diesen Gründen haben wir uns in diesem Anwendungsbereich für einen optischen Näherungsschalter entschieden. Dieser beinhaltet ein fertiges Modul bestehend aus einer Infrarot LED und einem Infrarot Fototransistor. Dieses Modul ist preiswert und leicht zu befestigen. \\Dadurch, dass unsere Anwendung keine genaue Abstandsmessung erfordert, wird keine zusätzliche Ansteuerung benötigt. Zur Stromversorgung reichen 5V Gleichspannung mit einem laut Datenblatt berechneten Vorwiderstand. Die Auswertung erfolgt durch einen digitalen Input-Pin des Raspberrys. Sobald sich eine Reflektorfläche vor dem Sensor bewegt, wird der Fototransistor niederohmig und ermöglicht einen Stromfluss. Dadurch liegt eine Spannung von 3,3V am Input-Pin an und wird vom Raspberry als HIGH-Zustand angesehen. Wenn die Reflektorfläche vom Modul nicht mehr erfasst wird, sperrt der Fototransistor, der Stromfluss wird unterbunden und am Input-Pin liegen nur mehr 0V an, was als LOW-Zustand angesehen wird. \\

Kennlinie des Sensors:

\begin{figure}[H]
  \begin{minipage}[hbt]{0.45\textwidth}
    
 	\caption{Diodenspannung zu \\Diodenstrom}
  	\label{Sens_vf_if}
  \end{minipage}
\hspace{.03\linewidth}
  \begin{minipage}[hbt]{0.45\textwidth}
    
  	\caption{Optische Übertragungs-\\stärke zu Diodenstrom}
  	\label{Sens_op_if}
  \end{minipage}
\end{figure}

\subsection{Ansteuerungen}
Da Variante 1 nur kurze Zeit verfolgt wurde, wurden genaue Ansteuerungen für Motoren und Hubmagnete nicht herausgesucht. Der Sensor benötigt keine zusätzliche Ansteuerung.
\newpage
\section{Variante 2}
\subsection{Aktoren}
\subsubsection{Hubmagnete}
Für die zweite Variante werden keine Hubmagnete benötigt.

\subsubsection{Motoren}
\begin{figure}[H] 
\begin{center}


\caption{Motor}
\label{Motor}

\end{center}
\end{figure}
Die Motoren wurden mithilfe folgender Kriterien ausgesucht: Preis, Drehzahl, Kraft, stromloses Verhalten und Spannung.
Wir haben uns  darauf festgelegt nur mit sicherer niedriger Gleichspannung zu arbeiten. Daher kommen nur Motoren mit einem Spannungsbereich von 0-24V in Frage. Aus diesem Grund werden die Auswahl eines Asynchronmotors ausgeschlossen. Die Anwendung fordert, dass sich die Motoren im stromlosem Zustand nicht bewegen lassen. Dadurch können folgende Motorarten ausgeschlossen werden: Synchronmotoren, reine Gleichstrommotoren, Schrittmotoren und Servomotoren, falls diese Motoren nicht über eine aktive Bremse verfügen. Ideal für unsere Anwendungen sind Gleichstrom-Schneckengetriebe-Motoren. Diese Motoren lassen sich aufgrund des mechanischen Aufbaus im stromlosem Zustand nicht drehen. Sie verfügen meistens auch über ein Getriebe, welches eine Übersetzung in eine niedrigere Drehzahl zur Folge hat. Gleichzeitig wird mit diesem Getriebe auch das Drehmoment erhöht, wodurch der Motor eine höhere Kraft aufbringen kann. Da Schneckengetriebemotoren in der Automobil Industrie als Scheibenwischermotoren verwendet werden, sind diese sehr preisgünstig zu erwerben.

\subsubsection{Lüfter}
\begin{figure}[H] 
\begin{center}


\caption{Lüfter}
\label{Luefter}

\end{center}
\end{figure}
Zur Kühlung des Raspberrys, findet ein externer 12V-Lüfter Verwendung, welcher einen Luftstrom um den Raspberry und den \ac{uC}ontroller erzeugt.
\subsection{Sensoren}
Der ausgewählte optische Sensor wurde in Variante 1 bereits beschrieben. Für genauere Informationen lesen Sie bitte in Punkt 4.3.2 nach.
Es werden zwei dieser Sensoren zur Positionierung verwendet. Der Sensor muss nur erkennen, ob sich eine Reflektorfläche vor ihm befindet. Bei der Futterschüsseldrehplatte wird am Rand der Scheibe, an der Position jeder Futterschüssel ein Reflektorstreifen verwendet. Dadurch kann mit der Software gezählt und erkannt werden, welche Futterschüssel sich aktuell vor dem Sensor befindet. Im Futterbeutelmagazin wird der Sensor dazu verwendet, um erkennen zu können, ob ein Futterbeutel für die Fütterung verfügbar ist. Wird vom Sensor, nach Drehen des Motors, kein weiterer Futterbeutel erkannt, wird von der Software, falls nötig, ein Fehler ausgegeben und der Benutzer informiert. Der Reflektorstreifen wird auf der Verschlussklemme jedes Futterbeutels befestigt.
\subsection{Ansteuerung}
Der Gesamtschaltplan wurde in ProfiCad realisiert. Der Schaltplan beinhaltet die Ansteuerung der Motoren und Sensoren, sowie die Visualisierung der Verkabelung der einzelnen Elemente.
Für ein einfacheres Verständnis wird der Gesamtschaltplan in kleinere Elemente aufgeteilt und in Unterpunkten beschrieben.
\newpage
\subsubsection{Motoransteuerung Variante 1}
Der Gleichstrom Schneckengetriebemotor in unserer Anwendung kann in beide Richtungen betrieben werden, je nach Polarität der Anschlüsse. Um eine softwaretechnisch einfache Ansteuerung ermöglichen zu können, wird oft eine H-Brücke zur Ansteuerung der Motoren verwendet. Diese H-Brücke besteht aus vier Transistoren. Für Motoren mit höheren Stromanforderungen werden MOSFET-Transistoren verwendet. Die Schaltung besteht aus zwei P-Kanal MOSFET T1, T3 und aus zwei N-Kanal MOSFET T2, T4. Die Schaltung laut Abbildung \ref{HBridge}, wurde aus dem Web\footfullcite{HBridge} entnommen und abgeändert. Dabei wurden die Bauteilwerte der MOSFETs und Teile der Schaltung übernommen. Der Raspberry steuert über Optokoppler die MOSFETs. Dabei wird über eine entsprechende Vorschaltung entweder das Gate vom MOSFET auf Ground- oder 12V-Potenzial gezogen. Zur Veranschaulichung wurden in Abbildung \ref{HBridge} die Raspberry Pins mit einer Klemme ersetzt, wobei die Klemme 1, T1, Klemme 2, T2, Klemme 3, T3 und Klemme 4, T4 steuert. 

Es gibt bei dieser Ansteuerungsart folgende erwünschte Zustände der Klemmen: \\
\begin{table}[htb]
\centering
\begin{tabular}{|c|c|c|c|c|c|} \hline
Klemme & Uhrzeigersinn & gegen Uhrzeigersinn & Auslaufen & Bremsen & Bremsen \\ \hline
1 & HIGH & LOW & LOW & HIGH & LOW  \\ \hline
2 & LOW & HIGH & LOW & LOW & HIGH \\ \hline
3 & LOW & HIGH & LOW & HIGH & LOW \\ \hline
4 & HIGH & LOW & LOW & LOW & HIGH \\ \hline
\end{tabular}
\caption{H-Brückenzustände}
\label{HBridge states}
\end{table}

Jede unterschiedliche Beschaltungsart als die oben angeführten, würde zu einem Kurzschluss führen und muss softwaretechnisch verhindert werden. \\

Kennlinie der Transistoren:

\begin{figure}[H]
  \begin{minipage}[hbt]{0.45\textwidth}
    
 	\caption{P-Kanal}
  	\label{Pchannel}
  \end{minipage}
\hspace{.03\linewidth}
  \begin{minipage}[hbt]{0.45\textwidth}
    
  	\caption{N-Kanal}
  	\label{Nchannel}
  \end{minipage}
\end{figure}

\begin{figure}[H] 
\begin{center}


\caption{H-Bridge}
\label{HBridge}

\end{center}
\end{figure}

Dieser Schaltplan dient nur als Beispiel-Schaltung und wurde aufgrund der Motoransteuerung Variante 2, nicht mehr weiter verfolgt. Um die Schaltung wirklich benutzen zu können, müsste eine Sicherung gegen einen Kurzschluss eingebaut werden. Für unsere Anwendung müsste eine Drehzahlregelung mittels PWM-Signal implementiert werden.
\newpage
\subsubsection{Motoransteuerung Variante 2}
\begin{figure}[H] 
\begin{center}


\caption{Motorsteuerung}
\label{Motoransteuerung}

\end{center}
\end{figure}
Aus sicherheits- und kostentechnischen Gründen, wurde von einer manuell gesteuerten H-Brücke auf ein fertiges Motorsteuerungsmodul umgestiegen. Der Vorteil dieser Ansteuerung besteht darin, dass ein Kurzschluss der H-Brücke hardwaretechnisch ausgeschlossen werden kann und damit nicht von der Software abgesichert werden muss. Das Motormodul verfügt außerdem über eine interne Strommessung für jeden der zwei unterstützten Motoren. Diese Messung kann bei Bedarf abgefragt werden. Für unsere Anwendung ist dies jedoch nicht erforderlich. Der Motortreiber unterstützt zwei Motoren, welche mit bis zu 30 Ampere bei 16V betrieben werden können, bevor der IC überhitzt oder andere Bauteile zerstört werden. Die Ansteuerung jedes Motors erfolgt über ein digitales Signal. Motor Nr.1 kann über den Pin AI0 aktiviert (enabled) werden. Dies dient zur Sicherung, dass der Motor nicht aus Versehen betätigt werden kann, solange der AI0 Pin nicht auf HIGH ist. Der enable Pin für Motor Nr.2 ist AI1. Um Motor Nr.1 im Uhrzeigersinn drehen zu lassen, muss der Pin D7 mit einem HIGH Signal und der Pin D8 mit einem LOW Signal angesteuert werden. Um Motor Nr.2 gegen den Uhrzeigersinn drehen zu lassen, muss der Pin D8 mit einem HIGH Signal und der Pin D7 mit einem LOW Signal angesteuert werden. Um den Motor Nr.1 bremsen zu können, muss Pin D8 und D7 mit entweder einem HIGH oder einem LOW Signal angesteuert werden. Für Motor Nr.2 ist die Funktionsweise gleich, jedoch muss der Pin D7 mit Pin D4 und Pin D8 mit Pin D9 ersetzt werden. Die externe Stromversorgung für den IC von 5V erfolgt über den VCC Pin. Die externe Stromversorgung für die Motoren erfolgt über den PWR Pin. Zusätzlich muss der GND Pin noch mit einem der beiden Ground Anschlüsse der externen Stromversorgungen verbunden werden. Motor Nr.1 wird über die Outputs A1 und B1 versorgt. Motor Nr.2 wird über die Outputs A2 und B2 versorgt. Beim Anschluss der Motoren muss auf die Polung geachtet und gegebenenfalls getestet werden, ob sich die Motoren auch wirklich beim Ansteuern der D7 oder D4 Pins im Uhrzeigersinn drehen und nicht gegen den Uhrzeigersinn. Falls beim Motor gekennzeichnet, sollte der Pluspol des Motors mit dem A1 beziehungsweise dem A2 Pin verbunden werden. Der Motortreiber verfügt auch über eine interne Drehzahlregelung, welche extra für beide Motoren über zwei \ac{PWM} Input Pins gesteuert werden kann. Die Drehzahl kann über den Duty Cycle des \ac{PWM} Signals geregelt werden.
\subsubsection{PWM-Signal-erzeugung für Motoransteuerung}
\begin{figure}[H] 
\begin{center}


\caption{PWM-Signal}
\label{PWM_Signal}

\end{center}
\end{figure}
Ein \ac{PWM} Signal ist ein periodisches Rechteck-Signal. Eine Periode wird als Duty Cycle bezeichnet. Dieser Duty Cycle enthält eine Prozentangabe, welche aussagt, wie viel Prozent des Duty Cycles HIGH und wie viel Prozent LOW sind. Ein Signal mit einem Duty Cycle von 100\% sagt aus, dass eine Periodendauer zu 100\% aus einem HIGH Signal und zu 0\% aus einem LOW Signal besteht. Ein Duty Cycle von 25\% sagt aus, dass eine Periode zu 25\% aus einem HIGH Signal und zu 75\% aus einem LOW Signal besteht. Das \ac{PWM} Signal kann von manchen ICs intern aufgenommen und der Duty Cycle ausgemessen werden. Dabei muss jedoch beachtet werden, dass die Frequenz des \ac{PWM} Signals nicht die maximale Schaltfrequenz des ICs übersteigt. In den meisten Fällen wird diese Frequenz, wie bei unserem Motortreiber, im Datenblatt angegeben. Das \ac{PWM} kann entweder über eigene ICs mit \ac{PWM} Generatoren oder \ac{uC}s mit internen \ac{PWM} Generatoren erzeugt werden. Das System muss nur über eine Echtzeitfähigkeit besitzen, damit der Duty Cycle keine Takte beim Zählen überspringen und nicht die Frequenz fehlerhaft werden kann. 
Unser \ac{PWM} Generator wurde mithilfe eines Arduino Nanos realisiert. Mithilfe des \ac{uC} Atmega328P wird der interne Zähler (Timer 2) dazu verwendet, einen Output Pin in den richtigen Abständen zu toggeln (von HIGH auf LOW oder umgekehrt schalten) um ein \ac{PWM} Signal zu erzeugen.

\begin{itemize}
\item verwendete Register:
\begin{itemize}
\item TCCR2A: Im TCCR2A Register wird festgelegt, in welchem Modus der Timer laufen soll und was mit den Pins OC2A und OC2B passieren soll, wenn der der aktuelle Timer-Wert mit einem der beiden Output Compare Register übereinstimmt. Die Bits COM2A1 und COM2A0 setzen im Fast-\ac{PWM} Modus fest, ob der OC2A Pin nicht beeinflusst wird und nicht verbunden ist, vom WGM22 Bit abhängig ist oder bei einem Compare Match, also wenn das Output Compare Register OCR2A mit dem aktuellen Timer Wert übereinstimmt, der OC2A Pin gesetzt und beim Reset des Timers resetet wird (non-inverting Mode), oder bei einem Compare Match der OC2A Pin resetet und beim Reset des Timers gesetzt wird (inverting Mode). \\ Die selbe Funktion haben die Bits COM2B1 und COM2B0, nur dass der Pin OC2B verändert und mit dem Compare Registe OCR2B verglichen wird. \\
Die Bits WGM21 und WGM20 setzen den Modus des Signalgenerators, die vom Timer unterstützt werden. Es gibt grundsätzlich drei Modi, in denen der Signalgenerator laufen kann: CTC, Fast \ac{PWM}, \ac{PWM} Phase Correct. \\
\begin{itemize}
\item Im CTC Modus kann der TOP Wert, zu dem der Counter zählt, immer bei jedem vollständigen Zählvorgang geändert werden. Der Zähler zählt in Form eines Sägezahn Signals und toggled den Pin immer, wenn der Top Wert erreicht wird.\\
\item Im Fast \ac{PWM} Modus zählt der Zähler in Form eines Sägezahnsignals und es wird bei jedem Zählschritt überprüft, ob der aktuelle Wert des Zählers mit dem Output Compare Register übereinstimmt. Was passiert, wenn die Werte übereinstimmen, wird in den COM2xx Bits festgelegt. Die Frequenz des Ausgangssignals am Pin kann nur über einen Prescaler verändert werden. Das bedeutet, dass die Frequenz nur sieben Frequenzen mit dem internen Timer annehmen kann. Das OCR2x Register kann während des Betriebes geändert werden. Damit kann der Duty Cycle während des Betriebes geändert werden. \\
\item Der \ac{PWM} Phase Correct Modus, lässt den Zähler von Bottom zu Top und wieder zu Bottom zählen. Das bewirkt, dass er Zähler in Form eines Dreiecksignals zählt. Somit ist das Ausgangs \ac{PWM} Signal immer symmetrisch um den BOTTOM und TOP Wert des Zählers. Daher bleibt das Signal immer Phasen-korrekt. Der Nachteil dieses Modus ist, dass er nur die halbe Frequenz des Fast \ac{PWM} Modus erreichen kann. Der \ac{PWM} Phase Correct Modus kann auch nur sieben Frequenzen annehmen.\\
\end{itemize} 
\item TCCR2B: Im TCCR2B Register wird für unsere Anwendung der Prescaler festgelegt, um die Frequenz des \ac{PWM}-Signales einzustellen. Dazu werden die Bits 0 bis 2 verwendet. Das sind die Bits CS20, CS21 und CS22. Die Bits FOC2A, FOC2B und WGM22 werden in unserer Anwendung nicht benötigt und können ignoriert werden. \\
\item OCR2A: Das Register OCR2A ist das Output Compare Match Register für den OC2A Pin. Das Register kann einen Wert zwischen 0 und 255 haben, wobei im Fast \ac{PWM} Modus 0 einem Duty Cycle von 0\% und 255 einem Duty Cycle von 100\% entspricht.\\
\item OCR2B: Das Register OCR2B ist das Output Compare Match Register für den OC2B Pin. Das Register kann einen Wert zwischen 0 und 255 haben, wobei im Fast \ac{PWM} Modus 0 einem Duty Cycle von 0\% und 255 einem Duty Cycle von 100\% entspricht.\\
\item DDRD: Im Register DDRD können I/O Pins als Output Pins gesetzt werden. Es muss nur das Bit des entsprechenden Pins gesetzt werden.\\
\item DDRB: Im Register DDRB können I/O Pins als Output Pins gesetzt werden. Es muss nur das Bit des entsprechenden Pins gesetzt werden.\\
\end{itemize}
\item Frequenz berechnen:\\
Die maximal Frequenz des \ac{PWM}-Signals für die Motoransteuerung beträgt 20kHz. Das bedeutet, dass man einen Frequenzwert so nahe wie möglich, aber unter der maximalen Frequenz wählen soll.\\
Berechnen lässt sich die Frequenz des \ac{PWM}-Signals mit folgender Formel:
\begin{align*}
f_{OC2xPWM}=\frac{f_{clk\_I/O}}{N*256} \\
\end{align*} 
f$_{OC2xPWM}$ ist die Frequenz, die das \ac{PWM}-Signal haben wird.\\
f$_{clk_I/O}$ ist die Taktfrequenz des Atmega328P, also 16MHz. \\
N ist der Wert des Prescalers, welcher im TCCR2B Register festgelegt wird. \\

\textbf{Frequenz Berechnung:}\\
$f_{OC2xPWM}$=$\frac{f_{clk\_I/O}}{N*256}$ = $\frac{16000000}{8 \cdot 256}$ = $\underline{7812,5Hz}$
\item Programm für Atmega328P: \\
\begin{lstlisting}[caption=$\mu$C-Programm,style=C]
void app_main (void)
{
  DDRD = (1<<PD3);
  DDRB = (1<<PB3);
  TCCR2A = (1<<COM2A1) | (1<<COM2B1) | (1<<WGM21) | (1<<WGM20);
  TCCR2B = (1<<CS21);
  OCR2A = 0x5f;
  OCR2B = 0x5f;
  
}
\end{lstlisting}
\newpage
\begin{itemize}
\item DDRD: Im DDRD Register wird der PD3 Pin auf Output geschaltet.
\item DDRB: Im DDRB Register wird der PB3 Pin auf Output geschaltet.
\item TCCR2A: Im TCCR2A Register wird der Non-Inverting Fast-\ac{PWM} Modus eingestellt für OC2A und OC2B. 
\item TCCR2B: Im TCCR2B Register wird der Prescaler festgelegt. 
\item OCR2A: Im OCR2A Register wird der Duty Cycle festgelegt. 0 entspricht 0\% und 255 entspricht 100\% 
\item OCR2B: Im OCR2B Register wird der Duty Cycle festgelegt. 0 entspricht 0\% und 255 entspricht 100\% 
\end{itemize}
\end{itemize}

Ein Signal, dass nach dem oben angeführten Programm generiert wird, sieht wie in Abbildung \ref{PWM} aus.
\begin{figure}[H] 
\begin{center}


\caption{PWM-Signal}
\label{PWM}

\end{center}
\end{figure}
\newpage
\subsubsection{Optokoppler}

Die Optokoppler in unserer Anwendung werden zur Potenzialerhöhung oder Potenzialverminderung von 3,3V auf 5V oder umgekehrt verwendet. Durch eine LED und einen Phototransistor werden die Schaltkreise getrennt. Wenn an der LED eine Spannung anliegt, beginnt sie zu leuchten und erhöht damit die Leitfähigkeit des Phototransistors. Dadurch ermöglicht ein Stromfluss der LED-Schaltung einen Stromfluss in der Phototransistor-Schaltung.

Kennlinie des Optokopplers:

\begin{figure}[H]
  \begin{minipage}[hbt]{0.45\textwidth}
    
 	\caption{Diodenstrom zu \\Diodenspannung}
  	\label{Opto_Vf_If}
  \end{minipage}
\hspace{.03\linewidth}
  \begin{minipage}[hbt]{0.45\textwidth}
    
  	\caption{Transistorstrom zu \\Transistorspannung}
  	\label{Opto_Vce_Ic}
  \end{minipage}
\end{figure}
\subsubsection{Gesamtschaltplan}
\begin{figure}[H]
\begin{minipage}[t]{6cm}
\vspace{0pt}
\centering

\caption{Blockschaltbild}
\label{Blockschaltbild}
\end{minipage}
\hfill
\begin{minipage}[t]{7cm}
\vspace{0pt}
Das Blockschaltbild vereinfacht die Gesamtschaltung und zeigt an, welche Bauteile miteinander verbunden sind. Die einzelnen Bauteile werden in den weiteren Punkten noch genauer beschrieben.
Verbindungen der Schaltpläne erfolgen mittels der Klemmen X1 bis X6.
\end{minipage}
\end{figure}

\subsubsection{Verkabelung der Motoransteuerung mit dazugehörigen Elementen}
\begin{figure}[H] 

\begin{center}


\caption{Motoransteuerung}
\label{Motoransteuerung}
\end{center}
\end{figure}
Die Motoransteuerung besteht aus folgenden Komponenten:\\
\begin{itemize}
\item Dem Motortreiber mit dem IC VNH2SP30.
\item Der Klemme X4, X3, X2, X1.
\item Sechs Optokopplern, welche die Ausgangsspannung von den GPIO-Pins auf 5V anheben.
\item Den beiden Motoren M1 und M2.
\item Den Widerständen R1 bis R6, welche den Strom begrenzen, damit der Optokoppler nicht überlastet wird.
\item Den Pulldown-Widerständen R7 bis R12 welche ein floaten, also eine fehlerhafte Spannung an den Input-Pins der Motorsteuerung verhindern sollen. \\
\end{itemize}
\newpage
\textbf{Genereller Ablauf:}
\begin{enumerate}
\item Der Arduino Nano erzeugt ein dauerhaftes \ac{PWM}-Signal, welches an die \ac{PWM}-Inputs D6 und D5, über die Klemme X4, der Motoransteuerung gelegt wird.
\item Die GPIO-Pins geben ein High-Signal über die Klemme X3, von 3,3V aus, welches die Optokoppler ansteuert. 
\item Der Optokoppler schaltet seinen internen Phototransistor durch und ermöglicht einen Stromfluss.
\item Der Strom fließt nun von der 5V Spannungsversorgung über die Klemme X2, über den Optokoppler in den Input-Pin der Motoransteuerung.
\item Je nach Ansteuerung der Pins, dreht sich einer oder beide Motoren im oder gegen den Uhrzeigersinn, oder werden gebremst. Dabei fließt ein Strom von der 12V Spannungsversorgung über die Klemme X1, über die Motoransteuerung zu den Motoren.
\item Die Motoransteuerung regelt die Spannung an den Motoren mittels des \ac{PWM}-Signals und regelt auch die Drehrichtung der Motoren je nach Ansteuerung.
\end{enumerate}
\textbf{Berechnungen:}
\begin{itemize}
\item R1 bis R6: \\
Die Spannung, die abfällt und der Strom, der fließt, kann aus dem Datenblatt des Optokopplers entnommen werden.\\
$U_{Optokoppler 5mA}=$1,15V \\
$U_{Optokoppler 10mA}=$1,2V \\
$I_{Optokoppler}$=5/10mA \\

\begin{center}
$R_{1,2,3,4,5,6}=\frac{U}{I}=\frac{U_{GPIO}-U_{Optokoppler 5mA}}{I_{Optokoppler}}=\frac{3,3V-1,15V}{0,005A}=430\Omega$
\end{center}

\begin{center}
$R_{1,2,3,4,5,6}=\frac{U}{I}=\frac{U_{GPIO}-U_{Optokoppler 10mA}}{I_{Optokoppler}}=\frac{3,3V-1,2V}{0,010A}=210\Omega$
\end{center}

Da der Ausgangsstrom durch den Eingangsstrom bestimmt wird, kann zur vereinfachten Berechnung durch die Kennlinie von Abbildung \ref{Opto_Vce_Ic} ein Eingangsstrombereich angenommen werden. Dadurch kann mithilfe der Kennlinie von Abbildung \ref{Opto_Vf_If} die abfallende Spannung am Optokoppler abgelesen werden. Mithilfe dieser Werte kann ein Widerstandsbereich berechnet werden, in dem der Widerstandswert liegen muss, damit der Ausgangsstrom hoch genug ist. Der berechnete Widerstandsbereich von $R_{1,2,3,4,5,6}$ beträgt 210$\Omega$-430$\Omega$. Es wird für diese Schaltung ein 390$\Omega$ Widerstand ausgewählt.
\end{itemize}

\subsubsection{Verkabelung des Sensors mit dazugehörigen Elementen} 
\begin{figure}[H] 
\begin{center}


\caption{Sensoransteuerung}
\label{Sensoransteuerung}

\end{center}
\end{figure}

Die Sensoransteuerung besteht aus folgenden Komponenten:
\begin{itemize}
\item Den optischen Sensoren OPB732WZ.
\item Der Klemme X2, X5, X6. 
\item Zwei Optokopplern, welche die Spannung der Sensoren von 5V auf ein 3,3V Potenzial bringen.
\item Den Widerständen R13 und R14, welche einen Spannungsabfall erzeugen, damit der Sensor nicht überlastet wird.
\item Den Widerständen R17 und R18, welche einen Spannungsabfall erzeugen, damit der Optokoppler nicht überlastet wird.
\item Den Pulldown-Widerständen R15 und R16 welche ein floaten, also eine fehlerhafte Spannung an den Input-Pins des Raspberrys verhindern sollen.\\
\end{itemize}
\newpage
\textbf{Genereller Ablauf:}
\begin{enumerate}
\item Wenn der Sensor eine Reflektor-Fläche vor sich erkennt, schaltet der Phototransistor im Sensor durch.
\item Der durchgeschaltete Phototransistor ermöglicht einen Stromfluss von der Spannungsquelle über die Klemme X2, in den Optokoppler.
\item Dadurch schaltet der interne Phototransistor des Optokopplers durch.
\item Der durchgeschaltete Phototransistor ermöglicht einen Stromfluss von einem der 3,3V-Pins über die Klemme X5, in einen der GPIO-Pins, über die Klemme X6 des Raspberrys.
\item Somit kann erkannt werden, welcher der Sensoren eine Reflektor-Fläche erkennt und weitere softwaretechnische Maßnahmen können erfolgen.
\end{enumerate}
\textbf{Berechnungen:}
\begin{itemize}
\item R17 und R18: \\
Die Spannung, die abfallen muss und der Strom, der fließt, kann aus den Datenblättern des Sensors und des Optokopplers entnommen werden.\\
$U_{Optokoppler 5mA}=$1,15V \\
$U_{Optokoppler 10mA}=$1,2V \\
$U_{CE(SAT)}=$0,4V \\
$I_{Optokoppler}$=5/10mA \\

\begin{center}
$R_{17,18}=\frac{U}{I}=\frac{U_{5V}-U_{Optokoppler 5mA}-U_{CE(SAT)}}{I_{Optokoppler}}=\frac{5V-1,15V-0,4V}{0,005A}=690\Omega$
\end{center}

\begin{center}
$R_{17,18}=\frac{U}{I}=\frac{U_{5V}-U_{Optokoppler 10mA}-U_{CE(SAT)}}{I_{Optokoppler}}=\frac{5V-1,2V-0,4V}{0,01A}=340\Omega$
\end{center}

Da der Ausgangsstrom durch den Eingangsstrom bestimmt wird, kann zur vereinfachten Berechnung durch die Kennlinie von Abbildung \ref{Opto_Vce_Ic} ein Eingangsstrombereich angenommen werden. Dadurch kann mithilfe der Kennlinie von Abbildung \ref{Opto_Vf_If} die abfallende Spannung am Optokoppler abgelesen werden. Mithilfe dieser Werte kann ein Widerstandsbereich berechnet werden, in dem der Widerstandswert liegen muss, damit der Ausgangsstrom hoch genug ist. Der berechnete Widerstandsbereich von $R_{17,18}$ beträgt 340$\Omega$-690$\Omega$. Es wird für diese Schaltung ein 680$\Omega$ Widerstand ausgewählt.
\newpage
\item R13 und R14:\\
Die Spannung die abfallen muss und der Strom der fließt, kann aus dem Datenblatt des Sensors entnommen werden.\\
$U_{F 50mA}=$1,45V \\
$U_{F 30mA}=$1,375V \\
$I_{F}$=30/50mA \\

\begin{center}
$R_{13,14}=\frac{U}{I}=\frac{U_{5V}-U_{F 50mA}}{I_{F}}=\frac{5V-1,45V}{0,05A}=72\Omega$
\end{center}
\begin{center}
$R_{13,14}=\frac{U}{I}=\frac{U_{5V}-U_{F 30mA}}{I_{F}}=\frac{5V-1,375V}{0,03A}=121\Omega$
\end{center}
Da die optische Übertragungsstärke durch den Eingangsstrom bestimmt wird, kann zur vereinfachten Berechnung durch die Kennlinie von Abbildung \ref{Sens_op_if} ein Eingangsstrombereich angenommen werden. Dadurch kann mithilfe der Kennlinie von Abbildung \ref{Sens_vf_if} die abfallende Spannung am Sensor abgelesen werden. Mithilfe dieser Werte kann ein Widerstandsbereich berechnet werden, in dem der Widerstandswert liegen muss, damit die optische Übertragungsstärke  hoch genug ist. Der berechnete Widerstandsbereich von $R_{13,14}$ beträgt 72$\Omega$-121$\Omega$. Es wird für diese Schaltung ein 100$\Omega$ Widerstand ausgewählt.
\item R15 und R16:\\
Diese Widerstandswerte werden mit 22k$\Omega$ angenommen.
\end{itemize}
\subsubsection{Spannungsversorgung}
\begin{figure}[H] 
\begin{center}


\caption{Spannungsversorgung Schaltplan}
\label{Spannungsversorgung}

\end{center}
\end{figure}
Die Spannungsversorgung erfolgt mittels eines 12V 400W Schaltnetzteils, welches aus 230V Wechselspannung 12V Gleichspannung erzeugt. Die 5V Versorgung erfolgt mittels eines 5V DC/DC Buck Down Converters.
Die Spannungen werden an die Klemmen X1 und X2 gelegt.

\subsubsection{Raspberry Verkabelung}
\begin{figure}[H] 
\begin{center}


\caption{Raspberry Schaltplan}
\label{Rasp_Circuit}

\end{center}
\end{figure}
Der Schaltplan zeigt, welche Raspberry-Pins mit welcher Klemme verbunden sind.
Die Pins werden mit den Klemmen X3, X5, X6 verbunden.
Der Raspberry wird über die Klemme X2 versorgt.

\subsubsection{Arduino Verkabelung}
\begin{figure}[H] 
\begin{center}


\caption{Arduino Schaltplan}
\label{Ard_Circuit}

\end{center}
\end{figure}
Der Schaltplan zeigt, welche Arduino Nano-Pins mit welcher Klemme verbunden sind.
Die Pins werden mit der Klemme X4 verbunden.
Der Arduino wird über die Klemme X2 versorgt.

\section{Mechanische Konstruktion}
\subsection{Motorhalterung Futterschüsseldrehplatte}
Der Motor der Drehplatte wird an der Spitze der Welle befestigt. Der Motor wird über die Motoraufnahme mit der Decke der Anlage verschraubt. Damit wird der Motor auf der richtigen Höhe gehalten und ist gegen Drehung gesichert. Die genauen Höhe der Platte kann noch nicht bestimmt werden, da die Gesamthöhe der Anlage und damit die Deckenhöhe nicht festgelegt wurde. Die Position der Befestigung auf der Decke ist noch nicht festgelegt, da die genaue Position der Wände der Anlage noch nicht festgelegt wurden und die Werte von diesen Positionen abhängig sind. Die Motoraufnahme wird mit drei M5 Schrauben an der Decke befestigt. Der Motor wird mit zwei M10 Schrauben mit Muttern an der Motoraufnahme befestigt.
\begin{figure}[H] 
\begin{center}

\caption{Motoraufnahme}
\label{Motoraufnahme}
\end{center}
\end{figure}
\newpage
\subsection{Motorhalterung Förderband}
Der Motor für das Förderband wird am Ende der Welle befestigt. Der Motor wird auf eine Aufnahme geschraubt und mithilfe eines Winkels an der rechten Stütze des Förderbandes befestigt. Die genaue Position variiert nach Förderbandlänge und muss nach Auslegung dimensioniert werden. Der Winkel wird mit drei M5 Schrauben an die Motoraufnahme geschraubt. Der Motor wird mit zwei M10 Schrauben mit Muttern an der Motoraufnahme befestigt. Der Winkel wird mit vier M6 Schrauben mit Muttern an der Förderbandstütze befestigt.
\begin{figure}[H] 
\begin{center}

\caption{Motorhalterung Förderband}
\label{Motor_mount_foerd}
\end{center}
\end{figure}
\subsection{Sensorhalterung Futterschüsseldrehplatte}

\begin{figure}[H]
\begin{minipage}[t]{6cm}
\vspace{0pt}
\centering

\caption{Sensorhalterung Drehplatte}
\label{Sens_Dreh}
\end{minipage}
\hfill
\begin{minipage}[t]{12cm}
\vspace{0pt}
Der Sensor der Drehplatte wird so nah wie möglich auf Höhe der Drehplatte befestigt. Der Sensor wird mit einer Holzleiste direkt auf die Grundplatte geschraubt. Der Sensor wird auf die Holzleiste mit zwei M2,5 Holzschrauben geschraubt und die Leiste wird mit zwei M2,5 Holzschrauben von der Unterseite der Grundplatte auf deren Oberseite verschraubt. Die genaue Position auf der Grundplatte kann noch variieren. Die Höhe der Holzleiste kann sich je nach Höhe der Futterschüsseldrehplatte verändern.
\end{minipage}
\end{figure}
\subsection{Sensorhalterung Förderband}
Der Sensor muss so nah wie möglich an der Klemme auf Höhe der Reflektorfläche befestigt werden. Der Sensor wird mit zwei Holzplatte an der linken Förderbandstütze befestigt. Der Sensor wird auf der ersten Holzleiste mit zwei M2,5 Holzschrauben befestigt. Die erste Holzleiste wird auf der zweiten Holzleiste mit zwei M2,5 Holzschrauben befestigt. Die zweite Holzleiste wird mit zwei M2,5 Schrauben und Muttern an die Förderbandstütze geschraubt. Die genaue Position kann variieren und muss in der Praxis ausgetestet werden. Die genauen Maße der Holzleisten und deren Befestigungen können noch variieren, je nach Größe der Stützen, der Befestigung des Förderbandes und weiteren Faktoren.

\begin{figure}[H]
  \begin{minipage}[hbt]{0.45\textwidth}
    
 	\caption{Sensorhalterung mit \\Position}
  	\label{Sens_halt_mit_gesamt}
  \end{minipage}
\hspace{.03\linewidth}
  \begin{minipage}[hbt]{0.45\textwidth}
    
  	\caption{Sensorhalterung}
  	\label{Sens_halt_allein}
  \end{minipage}
\end{figure}
\subsection{Halterung Raspberry}
Der Raspberry wird an die Unterseite des 7"  Touchdisplays befestigt. Das Touchdisplay selber wird in eine Vertiefung in der Decke der Anlage geschraubt. 
\subsection{Lüfterhalterung für Raspberry}
Der Lüfter wird am Ende eines Schachts, welcher sämtliche Elektronik, bis auf das 12V Schaltnetzteil, umschließt befestigt. Der Lüfter wird von der Innenseite an ein Loch in der Wand befestigt und von vier M4 Schrauben mit Muttern gehalten. Die genaue befestigung des Kanals und des Lüfters variiert noch je nach verfügbarem Platz. \\
\subsection{Förderband Stützen}

\begin{figure}[H]
\begin{minipage}[t]{6cm}
\vspace{0pt}
\centering

\caption{Förderband Stütze links}
\label{Foerd_stue}
\end{minipage}
\hfill
\begin{minipage}[t]{11cm}
\vspace{0pt}
Die Halterungen des Förderbandes sind in unserer Konstruktion überdimensioniert gezeichnet, da das Förderband je nach Benutzer eine gewünschte Länge annehmen kann. Die vier Halterungen aus Holz müssen daher standardmäßig eine Förderbandlänge von einem Meter tragen können. Die Halterungen sind mit zwei rechten Winkel an der Grundplatte befestigt. An der Oberseite der vorderen Halterungen ist eine extra Platte angeschraubt, die als Federbefestigung und Halterung der losen Walze dient. Für die Feder wird eine Schraube durch die Platte geschraubt, an der diese eingehängt wird. Für die Halterung der Walze wird ein Bolzen zwischen den beiden gegenüberliegenden Halterungen befestigt, an der zwei kleine Platten die Walzen an einer bestimmten Position halten. Unter der angeschraubten Platte wird ein Lager eingepresst um die Welle zu lagern wie in Abbildung \ref{Stuetz_Platte} zu sehen.  An den beiden hinteren Halterungen wird nur ein Lager für die Welle gepresst wie in Abbildung \ref{Stuetz_ohne_Platte} zu sehen.
\end{minipage}
\end{figure}
\begin{figure}[H]
  \begin{minipage}[hbt]{0.45\textwidth}
    
 	\caption{Stütze mit Platte}
  	\label{Stuetz_Platte}
  \end{minipage}
\hspace{.03\linewidth}
  \begin{minipage}[hbt]{0.45\textwidth}
    
  	\caption{Stütze ohne Platte}
  	\label{Stuetz_ohne_Platte}
  \end{minipage}
\end{figure}

\newpage
\section{Zusammenfassung und Selbstkritik}
\subsection{Relevante Meilensteine}
01.06.2017 Projektstart \\

13.10.2017 Grundkonzept Freeze\\

08.12.2017 Konstruktion + Elektronik fertig\\

02.03.2018 Dokumentation fertig\\ 
\subsection{Probleme}
\begin{itemize}
\item \textbf{Konstruktion:} Die ersten Konstruktionsvarianten stellten sich als viel zu aufwendig heraus, weshalb die geplante Zeit bis zum Grundkonzept Freeze nicht ausreichte und sich der Grundkonzept Freeze um Monate verschob. Des weiteren haben sich Probleme in der Elektronik ergeben, weshalb sich das Konzept der Elektronik auch nach dem Grundkonzept Freeze verändert hat.
\item \textbf{Elektronik:} Da ich versucht habe, so viel wie möglich von der Ansteuerung selbst zu machen, hat ein Großteil der Schaltung nicht funktioniert und musste verbessert oder ersetzt werden. 
\item \textbf{Dokumentation:} Das Einarbeiten in Latex hat mehr Zeit in Anspruch genommen als erwartet, weshalb sich das Ende der Dokumentation verzögerte.
\end{itemize}
\subsection{Zukünftige Verbesserungen}
\begin{itemize}
\item \textbf{Konstruktion:} Bei erneuter Arbeit an einem Projekt, sollten eher einfache Varianten verwendet werden, die gegebenenfalls noch verbessert und ergänzt werden können, als direkt mit einer schwierigen Variante zu beginnen, welche zu viel Zeit in Anspruch nimmt.
\item \textbf{Elektronik:} Bei der Elektronik muss ich in Zukunft versuchen eher bereits fertige Module für Schaltungen zu verwenden, als diese selbst zu entwerfen. Fertige Module sind meistens günstiger zu erwerben, als die einzelnen Bauteile und verfügen meist über zusätzliche Funktionen, welche die eigene Schaltung nicht bieten könnte. Als Beispiel wird die Motoransteuerung hergenommen. Die fertige Motoransteuerung ist günstiger als die selbst gezeichnete H-Brücke und verfügt zusätzlich über eine Drehzahlregelung mittels \ac{PWM}-Signal, internen Sicherungen gegen Kurzschlüsse und kann die Ströme der Motoren messen.
\item \textbf{Dokumentation:} Ich würde in Zukunft die Dokumentation parallel zur generellen Arbeit im Projekt beginnen, um eine Überforderung zum Schluss des Projektes zu vermeiden.
\end{itemize}
\subsection{Tatsächlicher Zeitpunkt der erreichten Meilensteine}
01.06.2017 Projektstart\\

10.03.2017 Grundkonzept Freeze\\

24.03.2018 Konstruktion + Elektronik fertig\\

27.03.2018 Dokumentation fertig\\
\section{Stückliste}
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

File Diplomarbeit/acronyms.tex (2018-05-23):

\begin{acronym}
	%Abkürzung hinzufügen: \acro{Kürzel}{Ausgeschrieben}
	\acro{HTTP}{HyperText Transfer Protocol}
	\acro{TCP}{Transmission Control Protocol}
	\acro{URI}{Uniform Resource Identifier}
	\acro{HTTPS}{HyperText Transfer Protocol Secure}
	\acro{npm}{Node Package Manager}
	\acro{HTML}{HyperText Markup Language}
	\acro{DOM}{Document Object Model}
	\acro{CSS}{Cascading Style Sheets}
	\acro{JSON}{JavaScript Object Notation}
	\acro{JWT}{\ac{JSON} Web Token}
	\acro{DBMS}{Database Management System}
	\acro{API}{Application Programming Interface}
	\acro{CLI}{Command Line Interface}
	\acro{CDN}{Content Delivery Network}
	\acro{WLAN}{Wireless Local Area Network}
	\acro{GUI}{Graphical User Interface}
	\acro{GPIO}{General Purpose Input/Output}
	\acro{pi4j}{Pi for Java}
	\acro{JNI}{Java Native Interface}
	\acro{JVM}{Java Virtual Machine}
	\acro{SPI}{Serial Peripheral Interface}
	\acro{UART}{Universal Asynchronous Receiver Transmitter}
	\acro{TCP/IP}{Transmission Control Protocol Internet Protocol}
	\acro{EDT}{Event Dispatch Thread}
	\acro{URL}{Uniform Resource Locator}
	\acro{CRLF}{Carriage Return Line Feed}	
	\acro{IP}{Internet Protocol}	
	\acro{uC}[$\mu$C]{Mikrocontroller}
	\acro{PWM}{Pulse Width Modulation}
\end{acronym}

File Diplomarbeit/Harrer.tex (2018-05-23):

\ihead{Florian Harrer}

\chapter{Java-Programm}
\label{sec:java-programm}

\section{Anforderungen}
\subsection{Programm}
Die Hauptaufgabe des Programms, welches am Raspberry Pi laufen soll, ist es, dem Benutzer eine Möglichkeit zum Steuern der Katzenfütterungsanlage zur Verfügung zu stellen. Weiters soll das Programm die Motoren steuern und die Sensoren in der Anlage auswerten können. Für diese Aufgabe sollen die \ac{GPIO} Pins am Raspberry verwendet werden.
\subsection{Design - Benutzerinterface}
Der Benutzer soll mit Hilfe eines kleinen Touchdisplays die Möglichkeit haben die Anlage zu steuern. Deswegen muss darauf geachtet werden, dass alle \ac{GUI} Fenster sinnvoll per Touch-Gesten verwendbar sind.
Das Design der \ac{GUI}-Fenster soll einfach und übersichtlich gestaltet werden. Auf der Hauptseite, also der Seite die immer zu sehen ist, sollen Informationen dargestellt werden, die dem Benutzer einen schnellen Überblick über den Zustand der Anlage geben. Alle anderen nicht direkt ersichtlichen Funktionen sollen über sinnvoll benannte Menüpunkte erreichbar sein.
\subsection{Externe Steuerung}
Da die Katzenfütterungsanlage die Katze füttern soll, wenn die Familie der Katze auf Urlaub ist, sollte die Anlage auch über das Internet erreichbar sein. Dafür gibt es die Möglichkeit einen Benutzer auf der Anlage anzulegen, mit welchem man anschließend über eine Webseite auf die Anlage zugreifen kann. Weiters soll das Java Programm (als Server) mit der Web-Applikation (als Client) über Sockets kommunizieren, also Daten austauschen können.

\newpage

\section{Voruntersuchung}
\subsection{Wieso Java und nicht C?}
Zu Beginn musste entschieden werden mit welcher Programmiersprache gearbeitet werden soll. Zur Auswahl standen Java und C, weil diese beiden Sprachen im Unterricht am stärksten behandelt wurden.
\\Vorteile von C:
\begin{itemize}
\item[•] Programme sind ressourcenschonender
\item[•] Hardwarenahe Programmierung einfach durchführbar, direkter Zugriff auf die Pins
\end{itemize}

Nachteile von C:
\begin{itemize}
\item[•] C ist nicht Multi-Threading fähig
\item[•] Die großen Freiheiten des Programmierers können zu einem unleserlichem Code führen
\end{itemize}

Vorteile von Java:
\begin{itemize}
\item[•] Erstellen einer \ac{GUI} mit Java Swing ist einfacher (weil es im Unterricht erlernt wurde)
\item[•] In Java kann nur sauber programmiert werden (aufgrund der Überprüfung des Compilers)
\end{itemize}

Nachteile von Java:
\begin{itemize}
\item[•] Java-Programme haben eine schlechtere Performance als C-Programme 
\end{itemize}

Nach dem Gegenüberstellen der Vor- und Nachteile wurde Java als Programmiersprache gewählt.

\subsection{Wieso das Raspberry Pi 3 Model B?}
Schon zu Beginn der Diplomarbeit war klar, dass mit einem Raspberry gearbeitet werden soll, weil bereits im Unterricht mit dem Raspberry gearbeitet wurde und weil an das Raspberry ein Display angeschlossen werden kann. Nun musste entschieden werden, welches Model verwendet werden soll.
\\ Technische Daten des Raspberry Pi 3 Model B:
\begin{itemize}
\item[•] Rechenleistung (CPU hat 4 Kerne und eine Taktfrequenz von 1,2GHz)
\item[•] Anzahl der \ac{GPIO}-Pins (26)
\item[•] \ac{WLAN} Fähigkeit
\end{itemize}

Technische Daten des Raspberry Pi 2 Model B:
\begin{itemize}
\item[•] Rechenleistung (CPU hat 4 Kerne und eine Taktfrequenz von 0,9GHz)
\item[•] Anzahl der \ac{GPIO}-Pins (26)
\item[•] keine \ac{WLAN}-Fähigkeit
\end{itemize}

Wir haben das Raspberry Pi 3 Model B, aufgrund der oben angeführten technischen Daten, gewählt. Den größten Einfluss auf die Entscheidung hatte dabei die \ac{WLAN}-Fähigkeit. Das liegt daran, dass dadurch die Anlage überall im Haus aufgestellt werden kann und keine Ethernetschnittstelle benötigt wird. Beim Raspberry Pi 2 ist es mit einem WLAN USB Device auch möglich eine WLAN-Verbindung herzustellen. Aber es ist uns wichtig, dass das Raspberry sich, ohne der Hilfe eines zusätzlichen Devices, mit dem WLAN verbinden kann. Ein weiterer positiver Aspekt des Raspberry Pi 3 ist die höhere Rechenleistung.

\subsection{Auswahl eines Touchdisplays}
Das Display muss folgende Anforderungen erfüllen:
\begin{itemize}
\item[•] Es muss ein Touchscreen-Display sein
\item[•] Es muss einfach an das Raspberry anschließbar sein
\item[•] Es soll nicht zu klein sein
\item[•] Es soll nicht zu teuer sein
\end{itemize}

Aufgrund dieser Anforderungen wurde das Touchdisplay von Raspberry gewählt.
\\ Folgende technische Daten des Display legten den Grundstein für die Entscheidung:
\begin{itemize}
\item[•] Das Anschließen des Displays an das Raspberry erfolgt über ein Displayportkabel und zwei Kabel für die Stromversorgung
\item[•] Das Display hat eine Größe von 7 Zoll
\item[•] Der Preis beträgt 70\euro{}
\end{itemize}

\subsection{Wieso pi4j?}
Da Java als Programmiersprache gewählt wurde, musste eine Möglichkeit die \ac{GPIO}-Pins anzusteuern gefunden werden.
Weil bei der Recherche außer \ac{pi4j} kaum etwas gefunden wurde, wurde \ac{pi4j} gewählt. Weiters vorteilhaft ist, dass das Ansteuern der Pins über die Java Software nicht sehr kompliziert ist. Hierfür müssen nur die Bibliotheken von \ac{pi4j} in das Projekt eingebunden werden.

\subsection{Wieso Mongodb?}
Eine Datenbank wurde gewählt, weil sie, gegenüber dem Speichern der Daten in eine Datei, mehrere Vorteile aufweist. 
\subsubsection{Vorteil gegenüber Daten in Datei speichern}
Vorteile einer Datenbank:
\begin{itemize}
\item[•] Professionellere Lösung als das Speichern in eine Datei
\item[•] Beim Speichern von großen Datenmengen effizienter
\item[•] Es kann vom Java Programm und vom Webserver zugegriffen werden, ohne dass es zu einem Fehler kommt, wenn ein DBMS mit Server verwendet wird
\item[•] Das Suchen von Daten ist einfacher
\end{itemize}
\subsubsection{Vergleich mit anderen Datenbanken}
Vergleich von Mongodb mit mySQL:
\begin{itemize}
\item[•] Mongodb
\begin{itemize}
\item[•] Mongodb ist schemenlos und open source
\item[•] Zugriffskonzept basiert auf \ac{JSON}
\item[•] Das Speichern von Daten mit einem stark strukturiertem Datenmodell ist einfach
\end{itemize}
\item[•] mySQL
\begin{itemize}
\item[•] mySQL hat ein Datenschema und ist nur teilweise open source (PostgreSQL ist open source)
\item[•] Zugriffskonzept auf mehrere Arten
\item[•] Unflexibel bei Daten mit einem stark strukturiertem Datenmodell
\end{itemize}
\end{itemize}
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

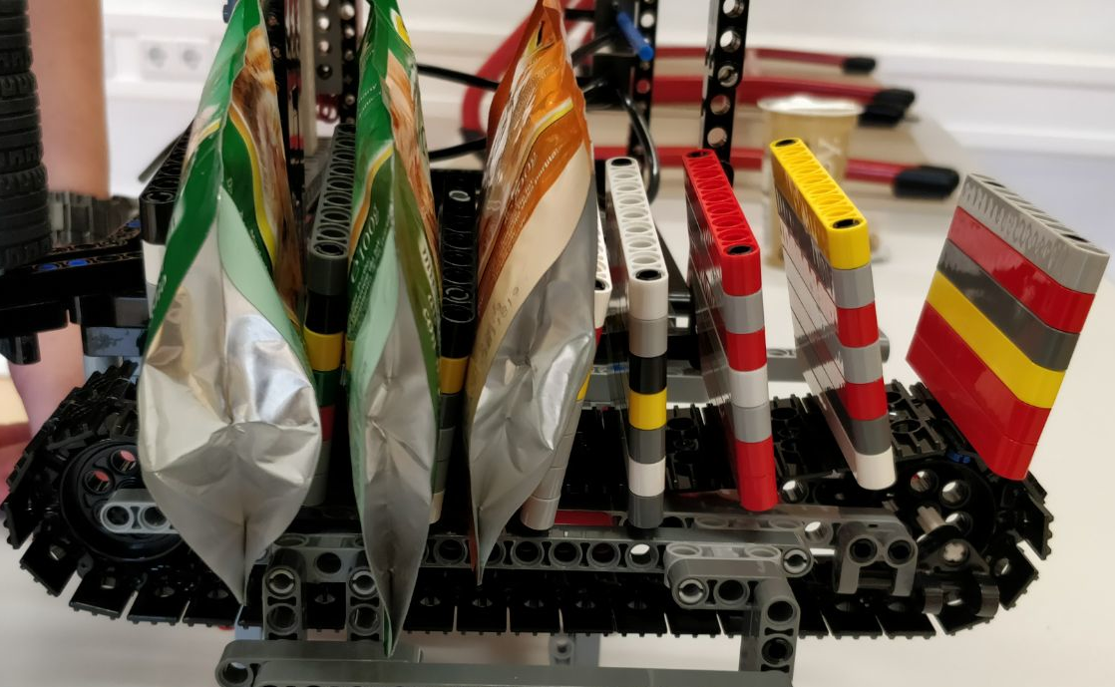
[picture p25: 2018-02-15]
Electronical/Dipl. Ing/Bilder/Ablauf_1_png/Magazin_Seitlich.png

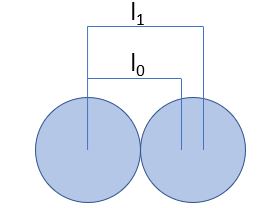
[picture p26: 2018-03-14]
Electronical/Dipl. Ing/Bilder/Powerpoint/Federkonstante.JPG

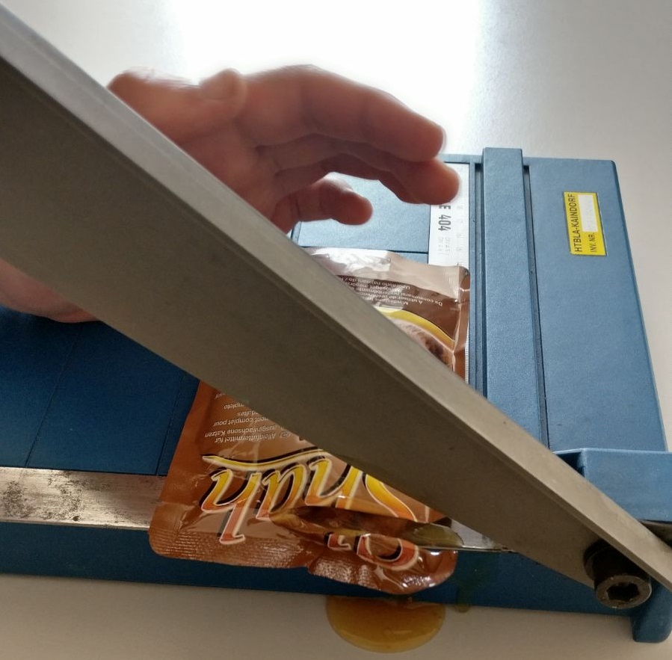
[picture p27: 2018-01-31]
Electronical/Dipl. Ing/Bilder/Schneideversuch_1.Art/Anfangsschnitt.jpeg

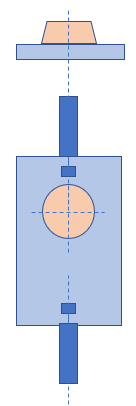
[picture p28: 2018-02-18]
Electronical/Dipl. Ing/Bilder/Powerpoint/Einschuessel_platte.PNG

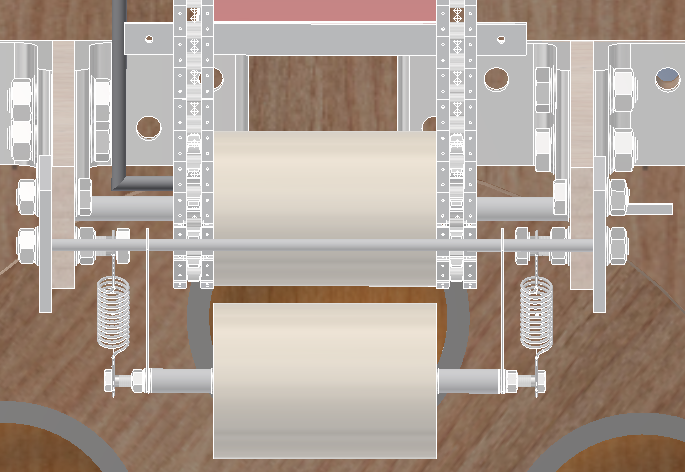
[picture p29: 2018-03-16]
Electronical/Dipl. Ing/Bilder/Inventor/Walzen_Ansicht.PNG

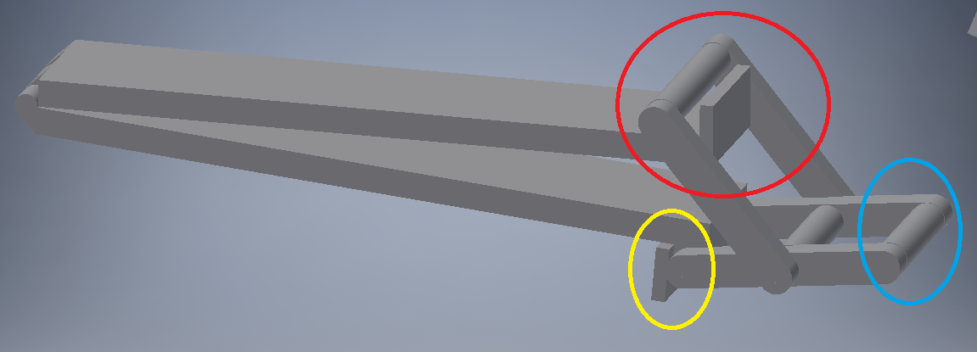
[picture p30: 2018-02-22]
Electronical/Dipl. Ing/Bilder/Inventor/Hebel_Klemme.PNG

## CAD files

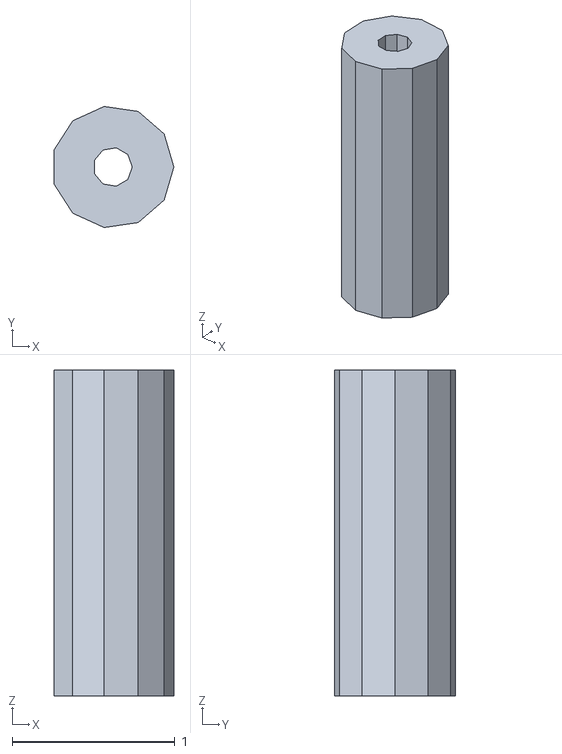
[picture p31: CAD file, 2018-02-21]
Mechanical/Inventorskizzen/Hebel_Röhre.stl
0.735 x 0.742 x 2.00

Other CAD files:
Mechanical/Inventorskizzen/Altes Schema/Futterschüssel_Platte.iam
Mechanical/Inventorskizzen/Altes Schema/Futterschüssel_außen.ipt
Mechanical/Inventorskizzen/Altes Schema/Futterschüssel_innen.ipt
Mechanical/Inventorskizzen/Antriebsscheibe.ipt
Mechanical/Inventorskizzen/Auspressrolle.ipt
Mechanical/Inventorskizzen/Auspressrolle_befaesstigung.iam
Mechanical/Inventorskizzen/Bolzen_228.ipt
Mechanical/Inventorskizzen/Draht.ipt
Mechanical/Inventorskizzen/Draht_Halterung.ipt
Mechanical/Inventorskizzen/Drehplatte_Rahmenvorrrichtung.ipt
Mechanical/Inventorskizzen/Feder.ipt
Mechanical/Inventorskizzen/Feder_Simulation.iam
Mechanical/Inventorskizzen/Flansch.ipt
Mechanical/Inventorskizzen/Fuehrungsschiene.ipt
Mechanical/Inventorskizzen/Futrterbeutel.ipt
Mechanical/Inventorskizzen/Futterschüssel_innen.ipt
Mechanical/Inventorskizzen/Förderband.iam
Mechanical/Inventorskizzen/Förderbandwelle_hinten.ipt
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

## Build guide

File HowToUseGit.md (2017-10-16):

* ## **git pull**

* ## git add -A

* ## git commit -m "Message"

* ## git push

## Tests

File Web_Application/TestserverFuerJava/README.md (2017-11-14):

# Testserver for Java Application

## Setup

Install the node modules needed to run the server:

```bash
npm install
```

## Starting the Server

To start the server simply type:

```bash
npm start
```

then open the browser on [localhost](http://localhost/api/callMeMaybe).

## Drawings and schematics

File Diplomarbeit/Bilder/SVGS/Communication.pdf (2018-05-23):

# Java Programm

# MongoDB

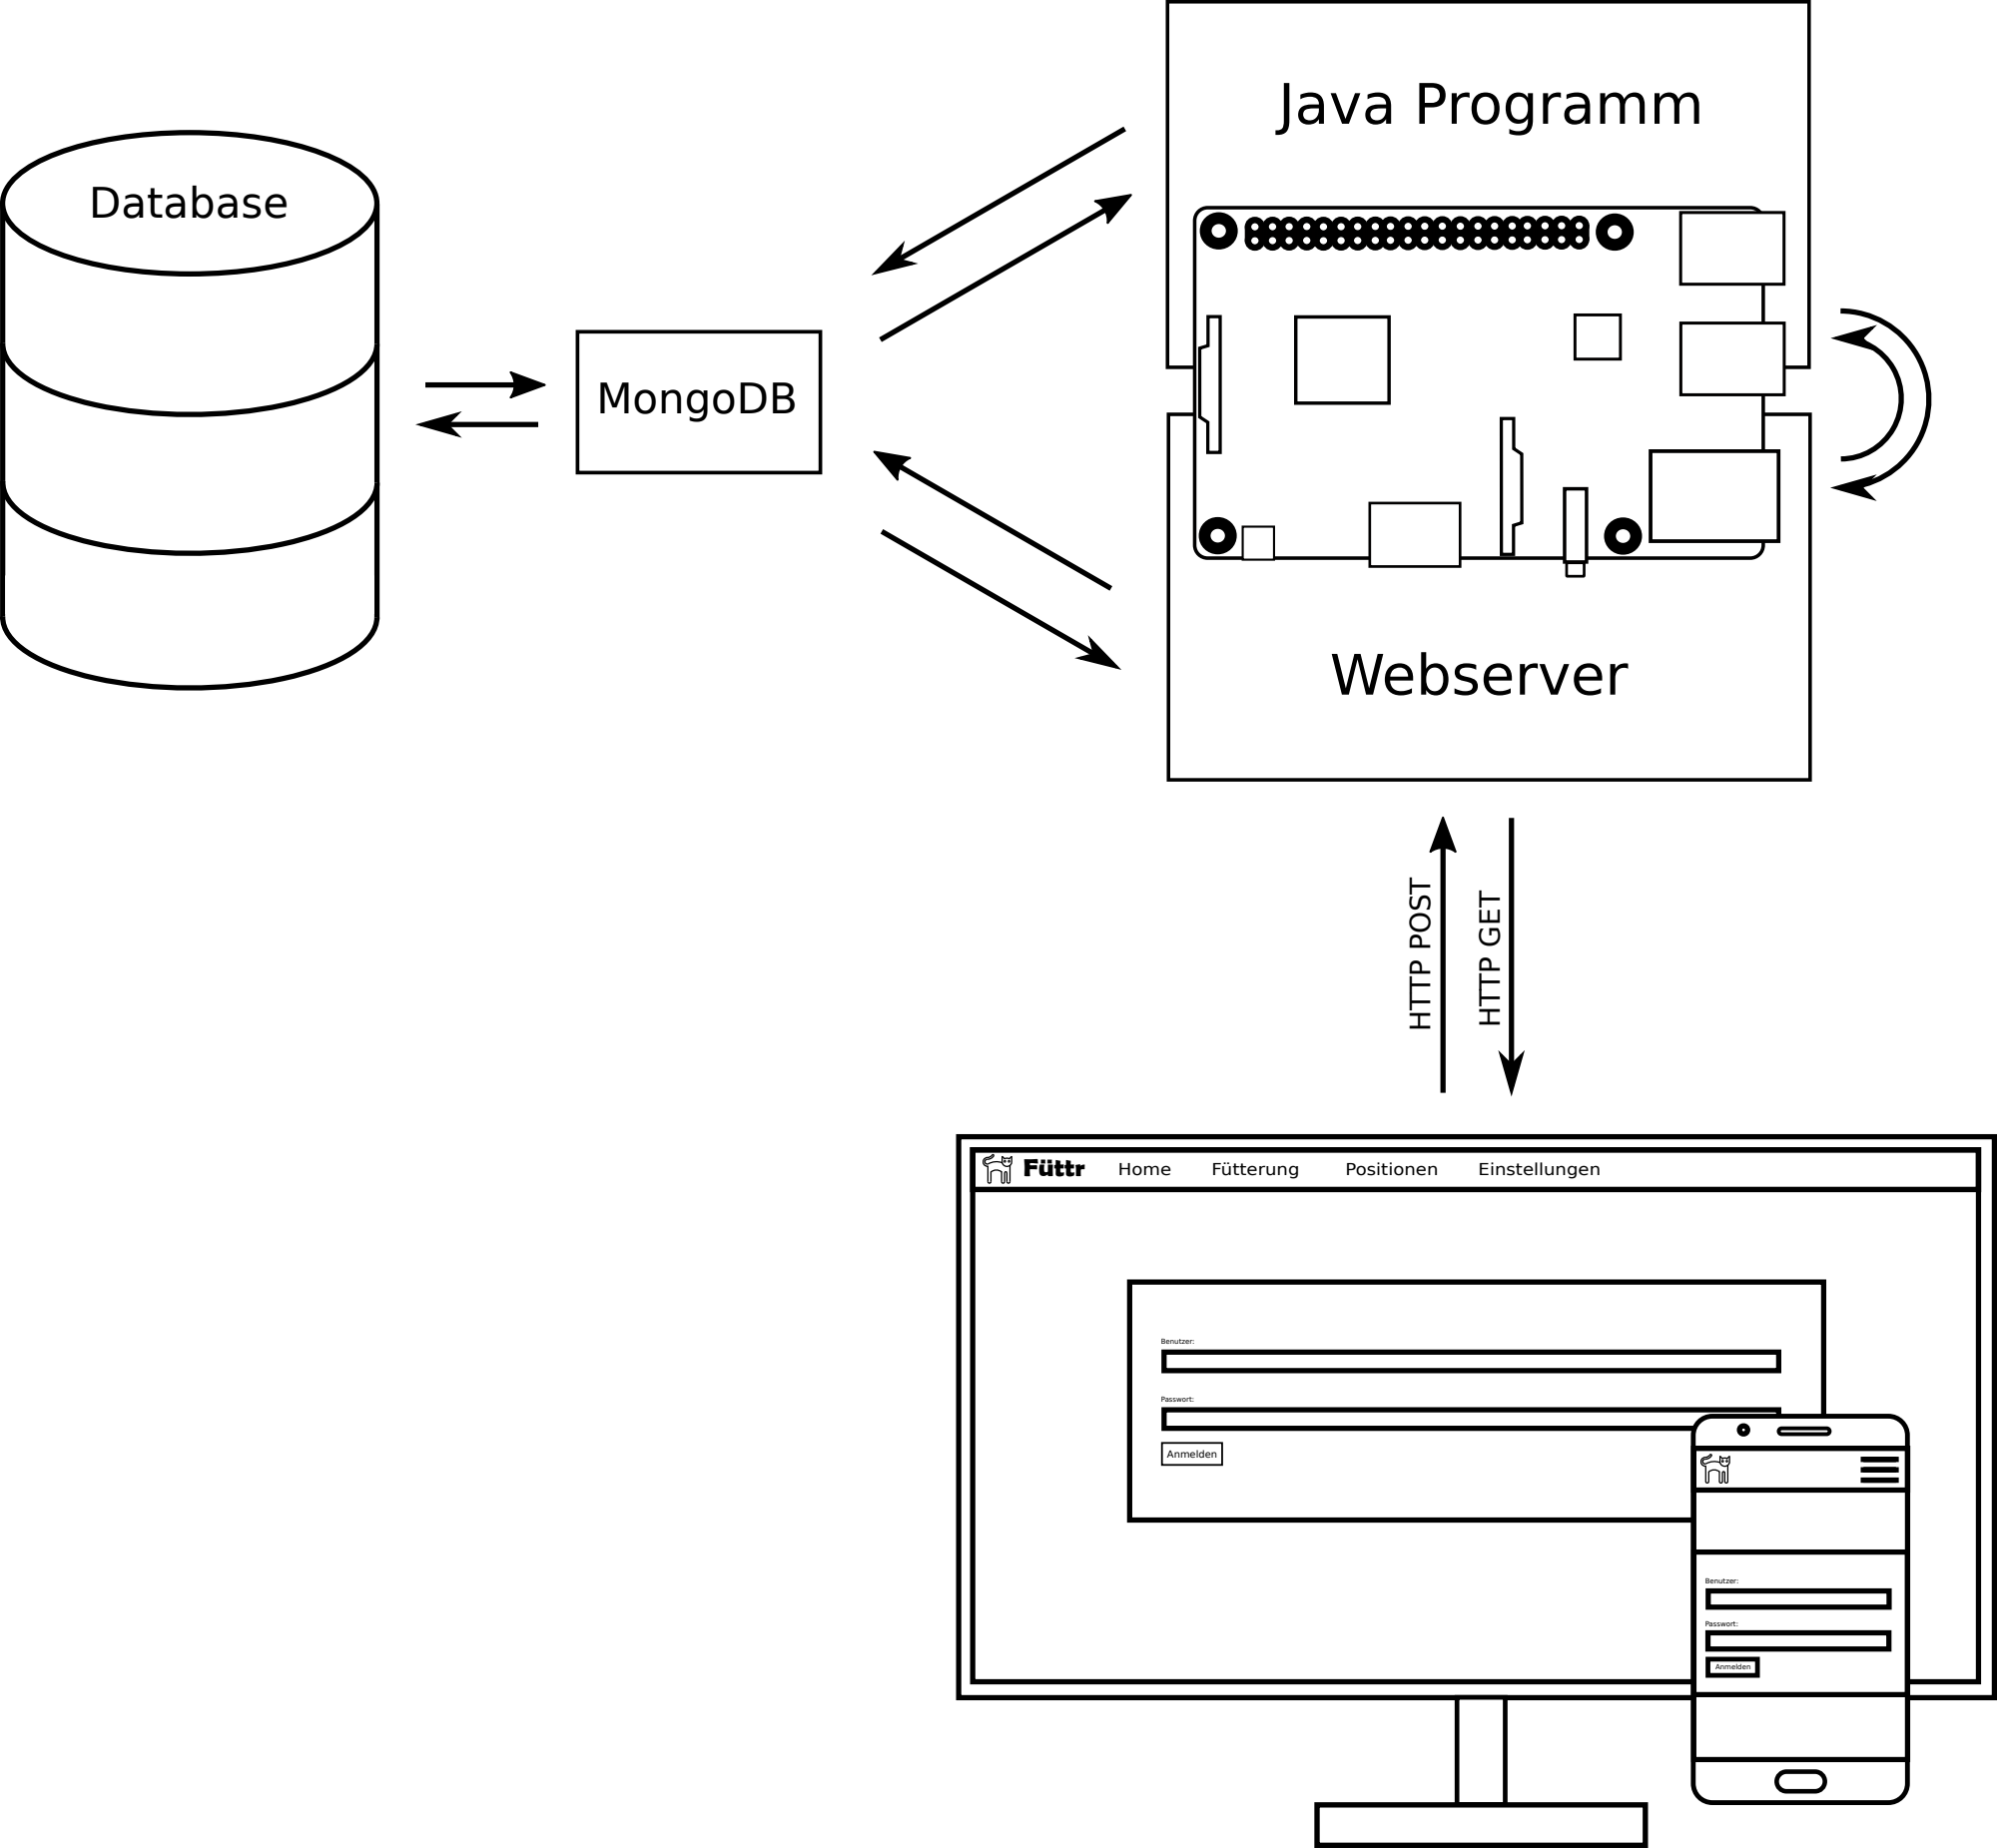
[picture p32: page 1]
Webserver; Füttr; Home; Fütterung; Positionen; Einstellungen; Benutzer:; Passwort:; Anmelden; HTTP POST; HTTP GET; Database

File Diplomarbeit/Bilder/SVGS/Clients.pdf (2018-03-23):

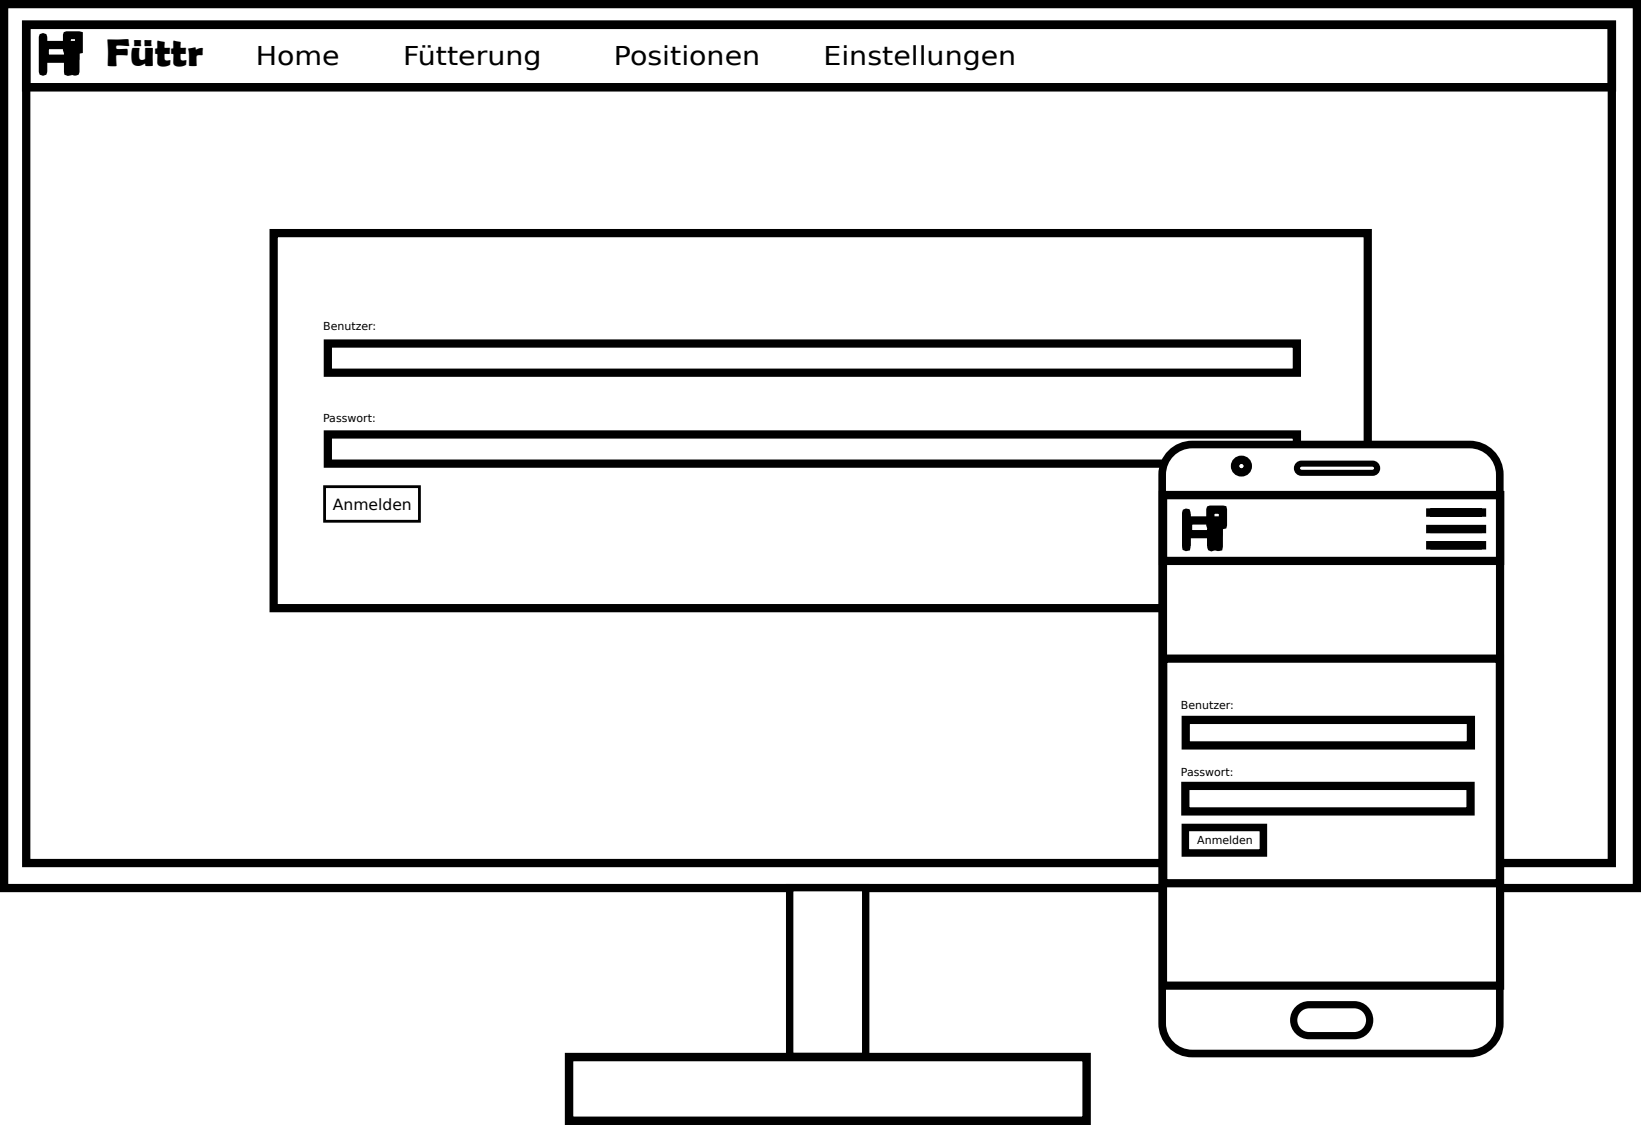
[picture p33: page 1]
Füttr; Home; Fütterung; Positionen; Einstellungen; Benutzer:; Passwort:; Anmelden

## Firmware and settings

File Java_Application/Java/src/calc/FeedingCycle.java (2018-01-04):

/*
 * To change this license header, choose License Headers in Project Properties.
 * To change this template file, choose Tools | Templates
 * and open the template in the editor.
 */
package calc;

// Controller
import com.pi4j.io.gpio.GpioController;
import com.pi4j.io.gpio.GpioFactory;
import com.pi4j.io.gpio.GpioPinDigitalOutput;
import com.pi4j.io.gpio.PinState;
import com.pi4j.io.gpio.RaspiPin;

//Listener
import com.pi4j.io.gpio.*;
import com.pi4j.io.gpio.event.GpioPinDigitalStateChangeEvent;
import com.pi4j.io.gpio.event.GpioPinListenerDigital;
import java.util.logging.Level;
import java.util.logging.Logger;


/**
 *
 * @author Florian
 */

/*
    Notification:
    sensor1: bowl
        GPIO_00
    sensor2: conveyor belt - feed bag
        GPIO_01
    engine1: bowl
        Transistor_1.1 GPIO_02
        Transistor_1.2 GPIO_03
        Transistor_1.3 GPIO_04
        Transistor_1.4 GPIO_05
    engine2: conveyor belt - feed bag
        Transistor_2.1 GPIO_06
        Transistor_2.2 GPIO_10
        Transistor_2.3 GPIO_08
        Transistor_2.4 GPIO_09

    1-4 -> clockwise
    2-3 -> counterclockwise

    transistor is active when voltage is supplied => pin state = high
    sensor return high when the object is in front of it
*/

public class FeedingCycle
{
    // 1. check if a feed bag is available
    
    // 2. check the position of the bowl
    
    // 3. move bowl to the filling location
    
    // 4. check the position of the bowl again
    
    // 5. check position of the feed  bag -> wrong position -> move conveyor belt
    
    // 6. move conveyor belt until the next feed bag reaches the sensor = filling the bowl
    
    // 7. move bowl to the feeding location
    
    public static void feed ()
    {
        // number of max usages 
        int maxbowlUsageIndex = 4;
        // number of usages
        int bowlUsageIndex = 0;
        
        Boolean wait = false;
        
        final GpioController gpio = GpioFactory.getInstance();
        
        // sensor2: conveyor belt - feed bag -> GPIO_01
        final GpioPinDigitalInput pin01 = gpio.provisionDigitalInputPin(RaspiPin.GPIO_01,PinPullResistance.PULL_DOWN);
        pin01.setShutdownOptions(true);
        
        // sensor1: bowl -> GPIO_00
        final GpioPinDigitalInput pin00 = gpio.provisionDigitalInputPin(RaspiPin.GPIO_00,PinPullResistance.PULL_DOWN);
        pin00.setShutdownOptions(true);
        
        // engine1: bowl -> Transistor_1.1 -> GPIO_02
        final GpioPinDigitalOutput pin02 = gpio.provisionDigitalOutputPin(RaspiPin.GPIO_02  ,PinState.HIGH);
        pin02.setShutdownOptions(true, PinState.LOW);
        
        // engine1: bowl -> Transistor_1.2 -> GPIO_03
        final GpioPinDigitalOutput pin03 = gpio.provisionDigitalOutputPin(RaspiPin.GPIO_03  ,PinState.HIGH);
        pin03.setShutdownOptions(true, PinState.LOW);
        
        // engine1: bowl -> Transistor_1.3 -> GPIO_04
        final GpioPinDigitalOutput pin04 = gpio.provisionDigitalOutputPin(RaspiPin.GPIO_04  ,PinState.HIGH);
        pin04.setShutdownOptions(true, PinState.LOW);
        
        // engine1: bowl -> Transistor_1.4 -> GPIO_05
        final GpioPinDigitalOutput pin05 = gpio.provisionDigitalOutputPin(RaspiPin.GPIO_05  ,PinState.HIGH);
        pin05.setShutdownOptions(true, PinState.LOW);
        
        // engine2: conveyor belt - feed bag -> Transistor_2.1 -> GPIO_06
        final GpioPinDigitalOutput pin06 = gpio.provisionDigitalOutputPin(RaspiPin.GPIO_06  ,PinState.HIGH);
        pin06.setShutdownOptions(true, PinState.LOW);
        
        // engine2: conveyor belt - feed bag -> Transistor_2.2 -> GPIO_07
        final GpioPinDigitalOutput pin07 = gpio.provisionDigitalOutputPin(RaspiPin.GPIO_10  ,PinState.HIGH); // use GPIO_10 instead of GPIO_7 because of error
        pin07.setShutdownOptions(true, PinState.LOW);
        
        // engine2: conveyor belt - feed bag -> Transistor_2.3 -> GPIO_08
        final GpioPinDigitalOutput pin08 = gpio.provisionDigitalOutputPin(RaspiPin.GPIO_08  ,PinState.HIGH);
        pin08.setShutdownOptions(true, PinState.LOW);
        
        // engine2: conveyor belt - feed bag -> Transistor_2.4 -> GPIO_09
        final GpioPinDigitalOutput pin09 = gpio.provisionDigitalOutputPin(RaspiPin.GPIO_09  ,PinState.HIGH);
        pin09.setShutdownOptions(true, PinState.LOW);
        
        Logger.getLogger("Start feeding").log(Level.INFO, "Start feeding");
        // 1. check if a feed bag is available
        if (pin01.getState() == PinState.HIGH)
        {
            String str = "cehck feed bag" + pin01.getPin() + "=" + pin01.getState(); 
            Logger.getLogger(str).log(Level.FINE, str);
            
            // 2. check the position of the bowl
            if (pin00.getState() != PinState.HIGH)
            {   
                str = "check bowl position" + pin00.getPin() + "=" + pin00.getState(); 
                Logger.getLogger(str).log(Level.FINE, str);
                
                // 3. move bowl to the filling location
                pin02.high();
                pin05.high();
                
                // position reached
                while (wait != true)
                {
                    if (pin00.getState() == PinState.HIGH)
                    {
                        pin02.low();
                        pin05.low();
                        
                        wait = true;
                    }
                }
                wait = false;
                
                Logger.getLogger("bowl position adjusted").log(Level.FINE, "bowl position adjusted");
            }
            
            // 4. check the position of the bowl again
            if (pin00.getState() == PinState.HIGH)
            {
                str = "check bowl position again" + pin00.getPin() + "=" + pin00.getState(); 
                Logger.getLogger(str).log(Level.FINE, str);
                
                // 5. check position of the feed  bag -> wrong position -> move conveyor belt
                // should be in position - according to the first check
                
                if (bowlUsageIndex < maxbowlUsageIndex)
                {                  
                    // move bowl back to the filling location
                    pin03.high();
                    pin04.high();
                    
                    //position reached
                    while (wait != true)
                    {
                        if (pin01.getState() == PinState.HIGH)
                        {
                            pin06.low();
                            pin09.low();
                            
                            wait = true;
                        }  
                    }
                    wait = false;
                    
                    Logger.getLogger("bowl moved back to feeding location").log(Level.FINE, "bowl moved back to feeding location");
                    
                    // 6. move conveyor belt until the next feed bag reaches the sensor = filling the bowl
                    pin06.high();
                    pin09.high();
                                        
                    // position reached
                    while (wait != true)
                    {
                        if (pin01.getState() == PinState.HIGH)
                        {
                            pin06.low();
                            pin09.low();
                            
                            wait = true;
                        }  
                    }
                    wait = false;
                    
                    // +1 to the number of usages
                    bowlUsageIndex++;
                    Logger.getLogger("feeding successful").log(Level.INFO, "feeding successful");
                }
                else
                {
                    // 6. move conveyor belt until the next feed bag reaches the sensor = filling the bowl
                    pin06.high();
                    pin09.high();
                    
                    // position reached
                    while (wait != true)
                    {
                        if (pin01.getState() == PinState.HIGH)
                        {
                            pin06.low();
                            pin09.low();
                            
                            wait = true;
                        }  
                    }
                    wait = false;
                    
                    // new bowl, number of usages = 0
                    bowlUsageIndex = 0;
                    
                    Logger.getLogger("feeding successful").log(Level.INFO, "feeding successful");
                }
            }
            else
            {
                // Sollte nie vorkommen
            }            
        }
        else
        {
            Logger.getLogger("No feeding bag left!").log(Level.SEVERE, "No feeding bag left!");
        }
        
        // shutdown gpio controller
        gpio.shutdown();
        Logger.getLogger("shutdown GPIO controller").log(Level.FINE, "shutdown GPIO controller");
    }

    public static void main(String[] args)
    {
        feed();
    }
    
}

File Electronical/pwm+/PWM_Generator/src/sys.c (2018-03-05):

#include "global.h"

#include <stdio.h>
#include <string.h>
#include <ctype.h>
#include <stdlib.h>

#include <avr/io.h>
#include <avr/interrupt.h>
#include <avr/wdt.h>
#include <util/delay.h>

#include "sys.h"
#include "app.h"

// defines


#ifdef __AVR_ATmega16__
  #define SYS_UART_BYTE_RECEIVED (UCSRA & (1<<RXC))
  #define SYS_UART_UDR_IS_EMPTY (UCSRA & (1<<UDRE))
  #define SYS_UDR UDR
  #define SYS_UART_RECEIVE_VECTOR USART_RXC_vect
  #define SYS_TIMER0_VECTOR TIMER0_COMP_vect
#elif __AVR_ATmega324P__
  #define SYS_UART_BYTE_RECEIVED (UCSR0A & (1<<RXC0))
  #define SYS_UART_UDR_IS_EMPTY (UCSR0A & (1<<UDRE0))
  #define SYS_UDR UDR0
  #define SYS_UART_RECEIVE_VECTOR USART0_RX_vect
  #define SYS_TIMER0_VECTOR TIMER0_COMPA_vect
#elif __AVR_ATmega328P__
  #define SYS_UART_BYTE_RECEIVED (UCSR0A & (1<<RXC0))
  #define SYS_UART_UDR_IS_EMPTY (UCSR0A & (1<<UDRE0))
  #define SYS_UDR UDR0
  #define SYS_UART_RECEIVE_VECTOR USART_RX_vect
  #define SYS_TIMER0_VECTOR TIMER0_COMPA_vect
#elif __AVR_AT90CAN128__
  #define SYS_UART_BYTE_RECEIVED (UCSR0A & (1<<RXC0))
  #define SYS_UART_UDR_IS_EMPTY (UCSR0A & (1<<UDRE0))
  #define SYS_UDR UDR0
  #define SYS_UART_RECEIVE_VECTOR USART0_RX_vect
  #define SYS_TIMER0_VECTOR TIMER0_COMP_vect

#endif

// declarations and definations

volatile struct Sys sys;

// functions

int sys_uart_putch (char c, FILE *f);
int sys_uart_getch (FILE *f);

static FILE mystdout = FDEV_SETUP_STREAM(sys_uart_putch, NULL, _FDEV_SETUP_WRITE);
static FILE mystdin  = FDEV_SETUP_STREAM(NULL, sys_uart_getch, _FDEV_SETUP_READ);

void sys_init (void)
{
  memset((void *)&sys, 0, sizeof(sys));
 _delay_ms(150);

#ifdef __AVR_ATmega16__
  OCR0  = (F_CPU+4)/8/10000-1;
  TCCR0 = (1 << WGM01) | (1 << CS01);
  TIMSK = (1 << OCIE0);
  TIFR  = (1 << OCF0);
  UBRRL = (F_CPU+8)/16/GLOBAL_UART_BITRATE-1;
  UBRRH = 0x00;
  UCSRA = 0x00;
  UCSRC = (1<<URSEL) | (1 << UCSZ1) | (1 << UCSZ0);
  UCSRB = (1 << RXCIE) | (1 << TXEN) | (1 << RXEN);

#elif __AVR_ATmega324P__
  OCR0A  = (F_CPU+4)/8/10000-1;
  TCCR0A = (1 << WGM01);
  TCCR0A = (1 << CS01);
  TIMSK0 = (1 << OCIE0A);
  TIFR0  = (1 << OCF0A);
  UBRR0L = (F_CPU/GLOBAL_UART_BITRATE + 4)/8 - 1;
  UBRR0H = 0x00;
  UCSR0A = (1<<U2X0);
  UCSR0C = (1 << UCSZ01) | (1 << UCSZ00);
  UCSR0B = (1 << RXCIE0) | (1 << TXEN0) | (1 << RXEN0);

#elif __AVR_ATmega328P__
  OCR0A  = (F_CPU+4)/8/10000-1;
  TCCR0A = (1 << WGM01);
  TCCR0B = (1 << CS01);
  TIMSK0 = (1 << OCIE0A);
  TIFR0  = (1 << OCF0A);
  UBRR0L = (F_CPU/GLOBAL_UART_BITRATE + 4)/8 - 1;
  UBRR0H = 0x00;
  UCSR0A = (1<<U2X0);
  UCSR0C = (1 << UCSZ01) | (1 << UCSZ00);
  UCSR0B = (1 << RXCIE0) | (1 << TXEN0) | (1 << RXEN0);

#elif __AVR_AT90CAN128__
  OCR0A  = (F_CPU+4)/8/10000-1;
  TCCR0A = (1 << WGM01);
  TCCR0A = (1 << CS01);
  TIMSK0 = (1 << OCIE0A);
  TIFR0  = (1 << OCF0A);
  UBRR0L = (F_CPU/GLOBAL_UART_BITRATE + 4)/8 - 1;
  UBRR0H = 0x00;
  UCSR0A = (1<<U2X0);
  UCSR0C = (1 << UCSZ01) | (1 << UCSZ00);
  UCSR0B = (1 << RXCIE0) | (1 << TXEN0) | (1 << RXEN0);

#endif

#ifdef SURE
  PORTA  =  0x0f;  // all LEDs off
  DDRA   =  0x0f;  // LEDs (PA3:0)
  DDRC  &= ~0xc0;  // Push Buttons SW1 (PC7) and SW2 (PC6)
#elif ARDUINO
  DDRB  = (1<< PB5); // LED L (yellow on pin PB5/SCK))
  PORTB = 0x00;
#elif ASURO
  PORTB &= ~0x01; // green LED off
  DDRB |= 0x01;   // green LED port (PB0) is output
  PORTD &= ~0x04; // red LED off
  DDRD |= 0x04;   // red LED port (PD2) is output
#elif CRUMB128
  DDRB  = (1<< PB7); // LED1 (green on pin PB7))
  PORTB = 0x00;
#endif

#ifdef GLOBAL_SURE_LCD
  PORTB  =    0x00;   // LCD-DATA
  PORTD  &= ~(0x1c);  // LCD E, R/W, RS
  DDRB   =    0xff;   // LCD-Data
  DDRD   |=  (0x1c);  // LCD-Data
  sys_lcd_init();
#endif
#ifdef  GLOBAL_SURE_SEG7
  PORTA  =  0x0f;  // all LEDs off
  DDRA   =  0xff;  // LEDs (PA3:0) and 7-Seg common cathode (PA7:0)
  PORTB  =  0x00;  // all 7-Seg anodes off
  DDRB   =  0xff;  // 7-Seg anodes
#endif


  // connect libc functions printf(), gets()... to UART
  // fdevopen(sys_uart_putch, sys_uart_getch);
  stdout = &mystdout;
  stdin  = &mystdin;
}


void sys_main (void)
{
}

//----------------------------------------------------------------------------

uint8_t sys_inc8BitCnt (uint8_t count)
{
  return count<0xff ? count+1 : count;
}


uint16_t sys_inc16BitCnt (uint16_t count)
{
  return count<0xffff ? count+1 : count;
}


void sys_sei (void)
{
  if (sys.flags_u8 & SYS_FLAG_SREG_I)
    sei();
}


void sys_cli (void)
{
  sys.flags_u8 |= (SREG & 0x80);
  cli();
}


void sys_newline (void)
{
  printf("\n\r");
}

//----------------------------------------------------------------------------

int sys_uart_getch (FILE *f)
{
  if (f != stdin)
    return _FDEV_EOF;
  if (sys.uart.wpos_u8 == sys.uart.rpos_u8) 
    return _FDEV_EOF;
  uint8_t c = sys.uart.rbuffer_u8[sys.uart.rpos_u8++];
  if (sys.uart.rpos_u8>=GLOBAL_UART_RECBUFSIZE)
    sys.uart.rpos_u8 = 0;
  return (int) c;
}


int sys_uart_putch (char c, FILE *f)
{
  if (f != stdout)
    return _FDEV_EOF;
  while (!SYS_UART_UDR_IS_EMPTY);
  SYS_UDR = c;
  return (int)c;
}


uint8_t sys_uart_available (void)
{
  return sys.uart.wpos_u8 >= sys.uart.rpos_u8
           ? sys.uart.wpos_u8 - sys.uart.rpos_u8
           : ((int16_t)sys.uart.wpos_u8) + GLOBAL_UART_RECBUFSIZE - sys.uart.rpos_u8;
}


//----------------------------------------------------------------------------

int16_t sys_uart_getBufferByte (uint8_t pos)
{
  int16_t value;
  sys_cli();

  if (pos >= sys_uart_available())
    value = -1;
  else
  {
    uint8_t bufpos = sys.uart.rpos_u8 + pos;
    if (bufpos >= GLOBAL_UART_RECBUFSIZE)
      bufpos -= GLOBAL_UART_RECBUFSIZE;
    value = sys.uart.rbuffer_u8[bufpos];
  }

  sys_sei();
  return value;
}


void sys_uart_flush (void)
{
  sys_cli();
  while (SYS_UART_BYTE_RECEIVED)
    sys.uart.rbuffer_u8[0] = SYS_UDR;

  sys.uart.rpos_u8 = 0;
  sys.uart.wpos_u8 = 0;
  sys.uart.errcnt_u8 = 0;
  sys_sei();
}


//****************************************************************************
// Event Handling
//****************************************************************************

Sys_Event sys_setEvent (Sys_Event event)
{
  uint8_t eventIsPending = 0;
  sys_cli();
  if (sys.eventFlag & event)
      eventIsPending = 1;
  sys.eventFlag |= event;
  sys_sei();

  return eventIsPending;
}


Sys_Event sys_clearEvent (Sys_Event event)
{
  uint8_t eventIsPending = 0;
  sys_cli();
  if (sys.eventFlag & event)
    eventIsPending = 1;
  sys.eventFlag &= ~event;
  sys_sei();

  return eventIsPending;
}


Sys_Event sys_isEventPending (Sys_Event event)
{
  return (sys.eventFlag & event) != 0;
}



//****************************************************************************
// 7 Segment Handling for Sure DEM2 Board
//****************************************************************************

#ifdef GLOBAL_SURE_SEG7
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

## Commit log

2017-10-12 pls dont die!
2017-10-13 initialize pichler
    [Antriebsscheibe.0002.ipt, Antriebsscheibe.ipt, Drehplatte_Rahmenvorrrichtung.0004.ipt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]
2017-10-24 button updated
2017-10-30 GUI und Kommunkikationsprotokoll
2017-10-30 Icons und StreamWriter_test und StreamReader_test
2017-10-30 StreamWriter_test und StreamReader_test
2017-10-30 StreamWriter_test und StreamReader_test 2
2017-10-31 posGUI und manSteuerGUI aktualisiert
2017-11-01 Zeiten in Hauptfenster anzeigen und aktualisieren
2017-11-02 Benutzer anlegen fast fertig und Geräteinformation (teilweise)
2017-11-06 Zeit umrechnen Methode hinzugefügt und .jar Datei
2018-01-04 feeding cycle updated - bowlIndex deleted & while loop added (sensor)
2018-01-08 Bilder hinzugefuegt
    [Fuehrungsschiene.0001.ipt, Fuehrungsschiene.ipt]
2018-01-09 pi4j test: pin übergeben
2018-01-09 Pi4Java Test: close connection to pin
2018-01-12 Zeitplan geaddet
    [Arbeitszeiten.xlsx]
2018-01-19 Inventor Rolle update
    [Auspressrolle.0001.ipt, Auspressrolle.0005.ipt, Auspressrolle.ipt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]
2018-01-26 Inventor Update
    [Auspressrolle.0005.ipt, Auspressrolle.0006.ipt, Auspressrolle.ipt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]
2018-01-29 pico headed
2018-02-20 LaTeX Text und übersetzt
2018-02-21 hebel update
    [Hebel_KLemme_Hebel.0001.ipt, Hebel_KLemme_Hebel.0004.ipt, Hebel_KLemme_Hebel.ipt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]
2018-02-22 git commit -m "la"
2018-03-01 Pico formatted
2018-03-05 Simulation update
    [Flansch.0003.ipt, Flansch.0004.ipt, Flansch.ipt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]
2018-03-05 PWM update
2018-03-12 I push my fingers into my eyes+
2018-03-16 Inventor Bilder
    [Förderband.0024.iam, Förderband.0025.iam, Förderband.iam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]
2018-03-23 steck sie rein und zieh sie raus
2018-03-24 Bilder und Latex update
2018-03-27 generelle updates
    [Förderband.0025.iam, Förderband.0026.iam, Förderband.iam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]
2018-03-27 i push my fingers into my eyes
2018-03-28 wirklich vorletzter push
2018-05-23 PowerPoint roh Entwurf
2018-05-24 Powerpoint update
    [Förderband.0027.iam, Förderband.0028.iam, Förderband.iam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]
2018-05-25 Harrer Text und Präsentation
2018-05-27 Harrer Text und Powerpoint
